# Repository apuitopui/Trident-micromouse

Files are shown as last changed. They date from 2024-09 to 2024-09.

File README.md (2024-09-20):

# TRIDENT - Classic size micromouse
Trident is a robotic project to compete in [classic size micromouse](https://www.ntf.or.jp/). 
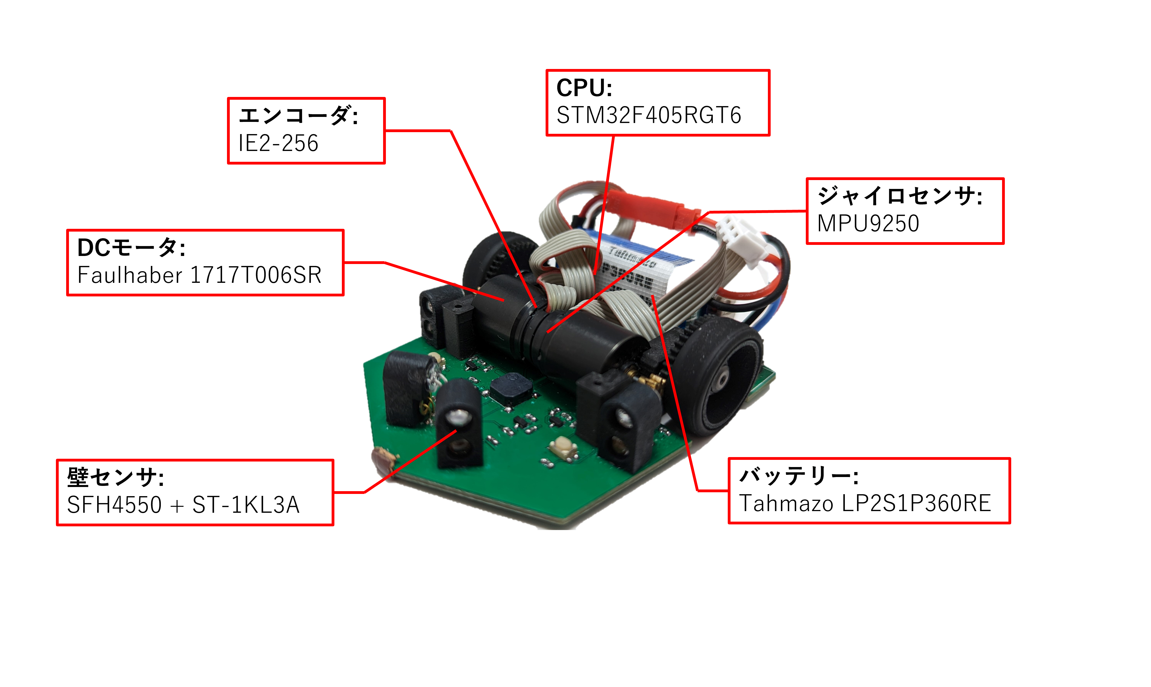
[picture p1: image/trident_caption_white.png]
Trident


## Circuit
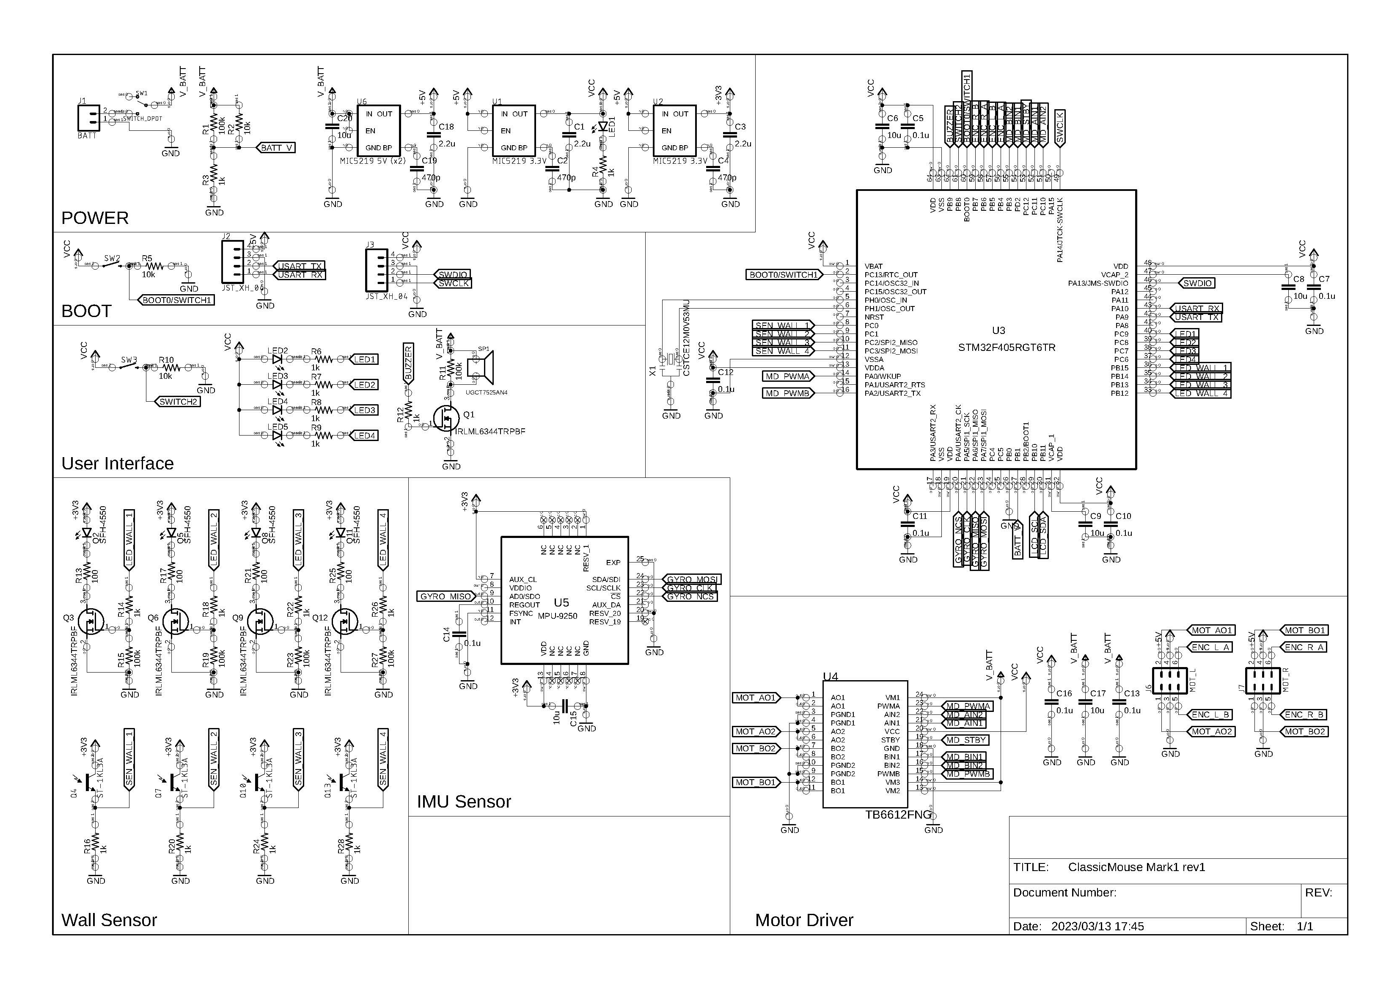
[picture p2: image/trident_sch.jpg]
Schematic


## Specification
|Specification|Value| 
|---|---|
|Size(W x L x H)| 70 x 84 x 30mm |
|Weight|About 100g|
|CPU|STM32F405RGT6|
|Battery|Tahmazo LP2S1P360RE|
|Motor|Faulhaber 1717T006SR|
|Encoder|IE2-256|
|Motor driver|TB6612FNG|
|Pinion|M0.5 9T Brass|
|Spur Gear|M0.5 42T PA12 MJF|
|Tire|Kyosho high grip tire|
|Gyro rensor|MPU9250|
|Wall sensor LED|SFH4500|
|Wall sensor Phototransistor| ST-1KL3A|

## Environment 
* IDE : STM32 Cube IDE
* EDA : Autodesk Eagle
* CAD : Autodesk Fusion

## Joined micromouse competition
|Date|Competition|Best time|Rank|
|---|---|---|---|
|2023/02/19|第43回全日本マイクロマウス大会|0:18.822|7|
|2023/09/24|第４０回マイクロマウス北陸信越地区大会|0:11.231|5|
|2023/11/12|第３９回マイクロマウス東日本地区大会|0:10.233|8|
|2023/12/09|第３７回全日本学生マイクロマウス大会|0:08.502|8|
|2023/02/18|第44回全日本マイクロマウス大会|0:09.356|14|

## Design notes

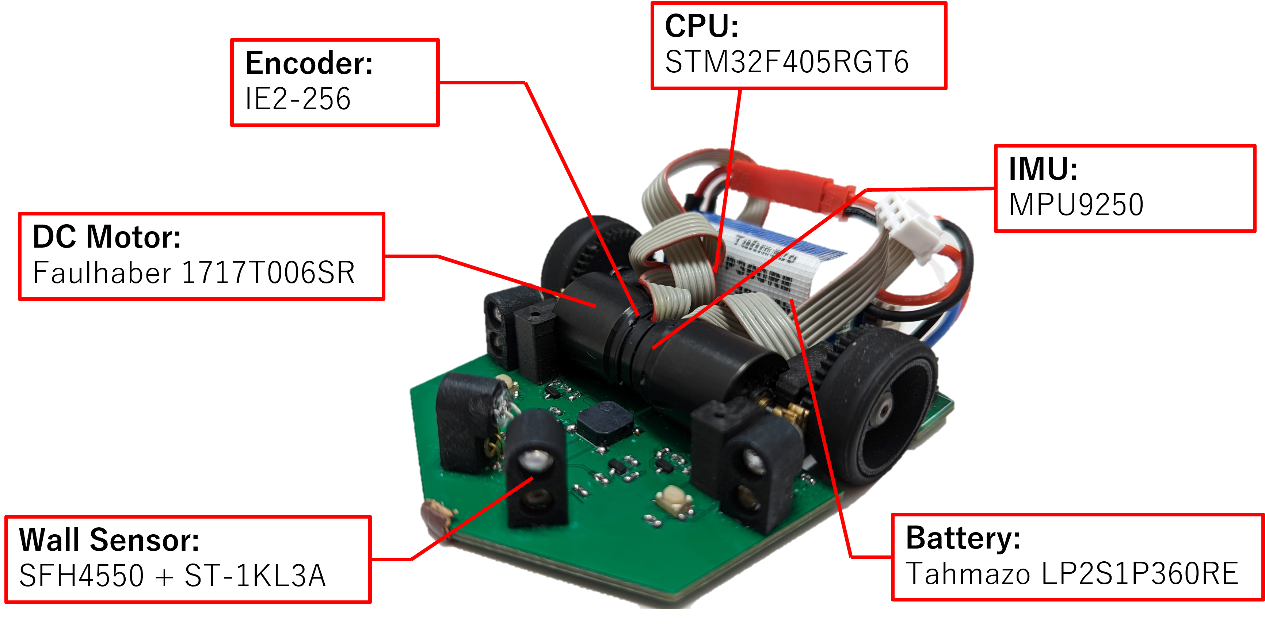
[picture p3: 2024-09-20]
image/trident_caption.png

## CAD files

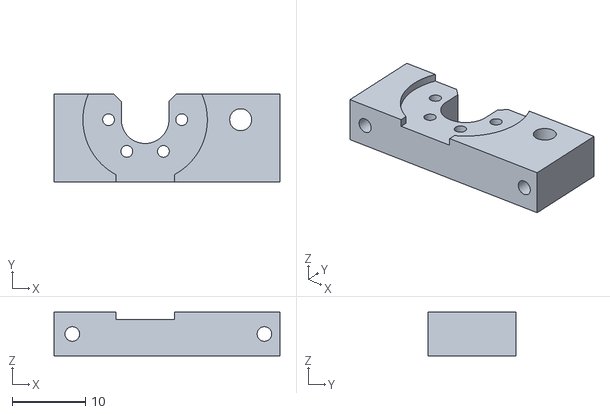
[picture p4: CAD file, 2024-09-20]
hardware/Trident M1 rev1 R.stl
30.9 x 12.0 x 6.00

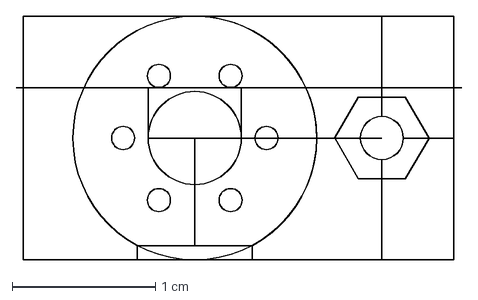
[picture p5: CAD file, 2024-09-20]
hardware/print2 v2.dxf
3.11 x 1.70 cm

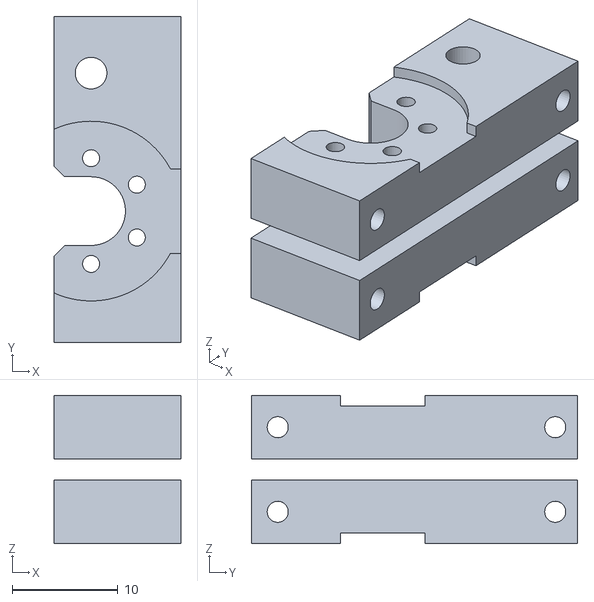
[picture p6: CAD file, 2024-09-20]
hardware/print3 v1.stl
12.0 x 30.9 x 14.0

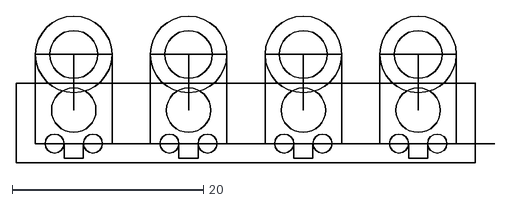
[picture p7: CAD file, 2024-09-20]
hardware/SensorMount.dxf
50.0 x 15.3

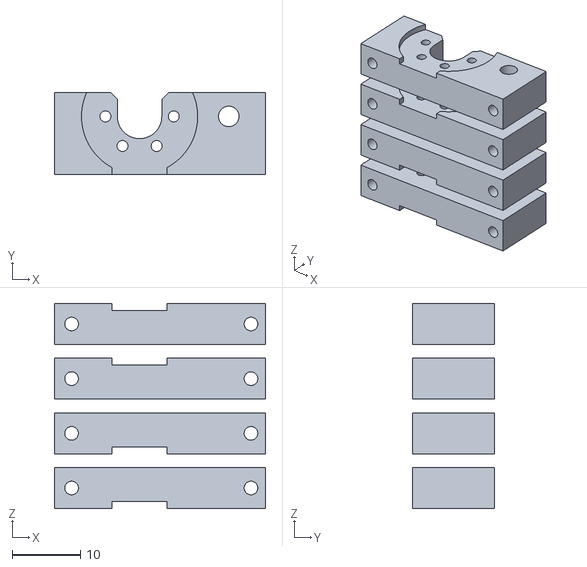
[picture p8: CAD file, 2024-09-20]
hardware/Trident M1 rev1Mount.stl
30.9 x 12.0 x 30.0

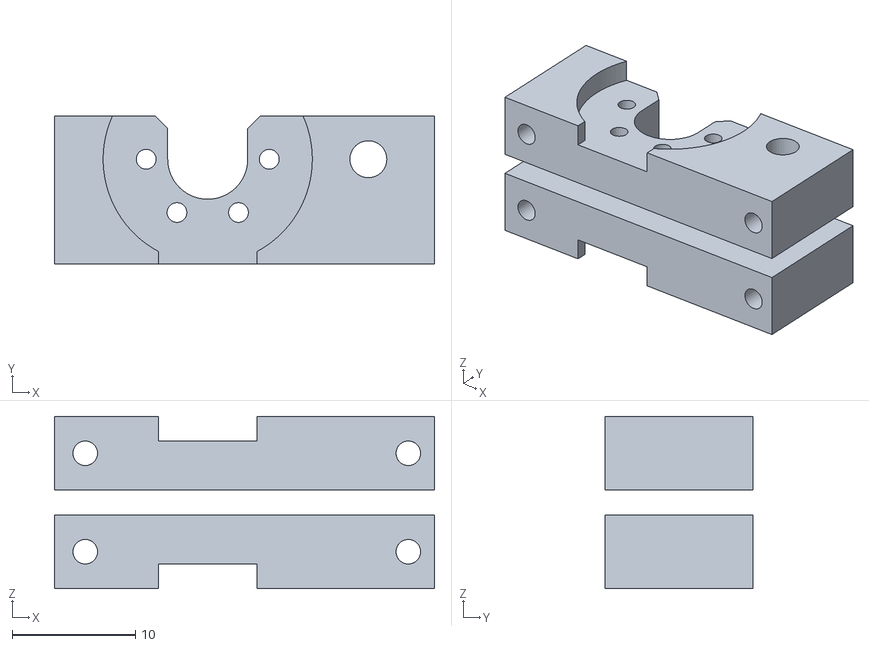
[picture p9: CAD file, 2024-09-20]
hardware/Trident M1 rev1 Mount2.stl
30.9 x 12.0 x 14.0

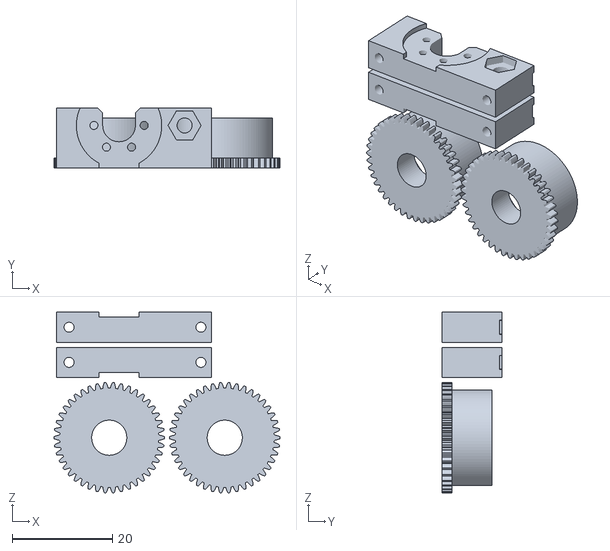
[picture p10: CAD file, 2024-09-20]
hardware/221201 - WheelMount.stl
45.0 x 12.0 x 36.0

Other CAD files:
hardware/無題 v2.dxf
hardware/Trident M1 rev1 L.stl
hardware/Trident M1 rev1 LR.stl
hardware/221204 - WheelMount.stl
hardware/Trident M1 rev1 Mount2.f3z
hardware/Trident Mark1 rev1 Mount.f3z

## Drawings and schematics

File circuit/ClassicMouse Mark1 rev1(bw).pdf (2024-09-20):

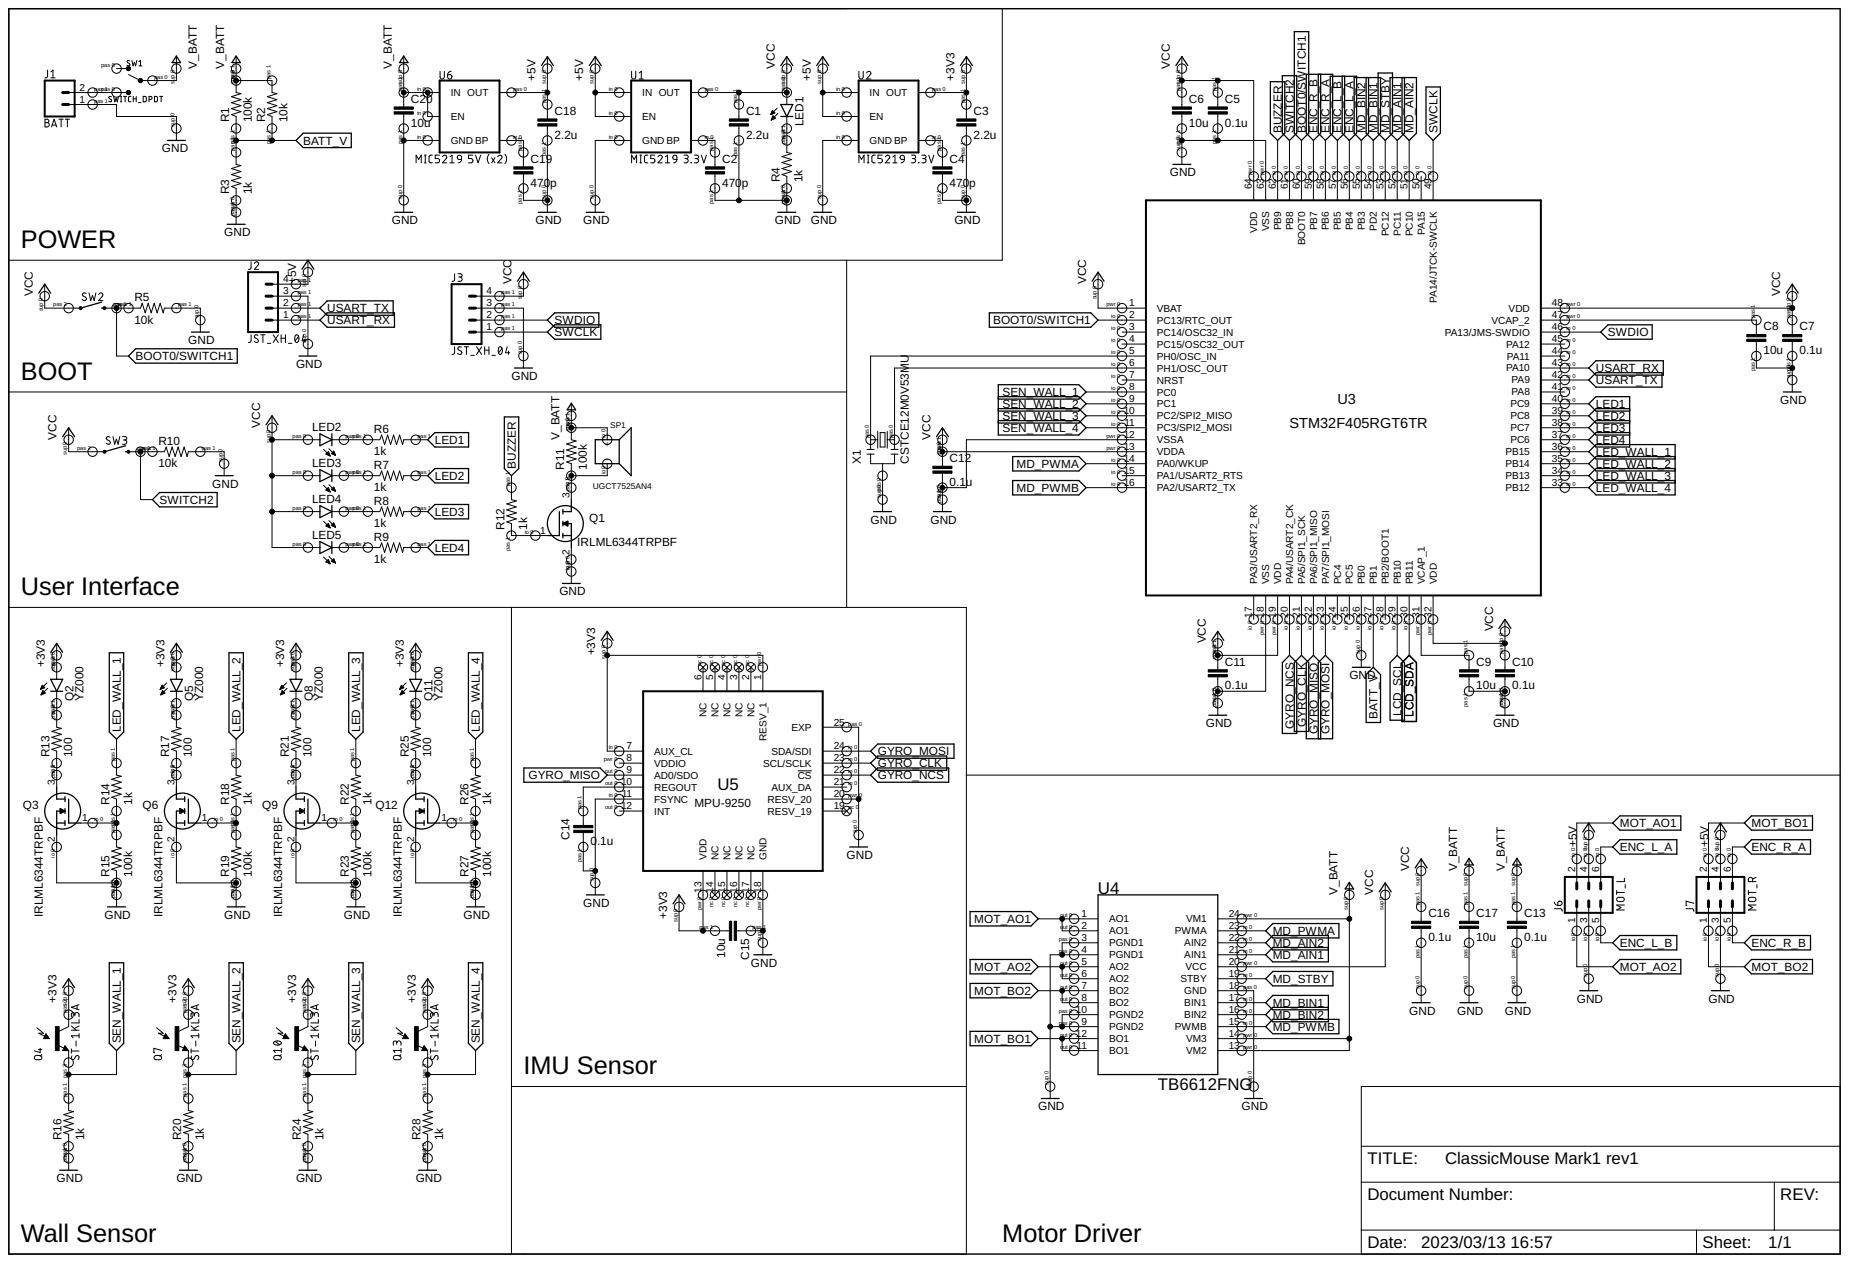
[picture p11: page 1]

pas 0 pas 0 pas 1 pas 1

pas 1 pas 1 sup 0 sup 0

io 0 io 0 pas 1 pas 1

pas 1 pas 1 pas 1 pas 1up 0

23 VM1 in 0 MD_PWMA

pas 0 | 21 AIN2 MD_AIN2 in 0

19 VCC in 0 MD_STBY

pas 1 pas 1up 0 pas 3 pas 2

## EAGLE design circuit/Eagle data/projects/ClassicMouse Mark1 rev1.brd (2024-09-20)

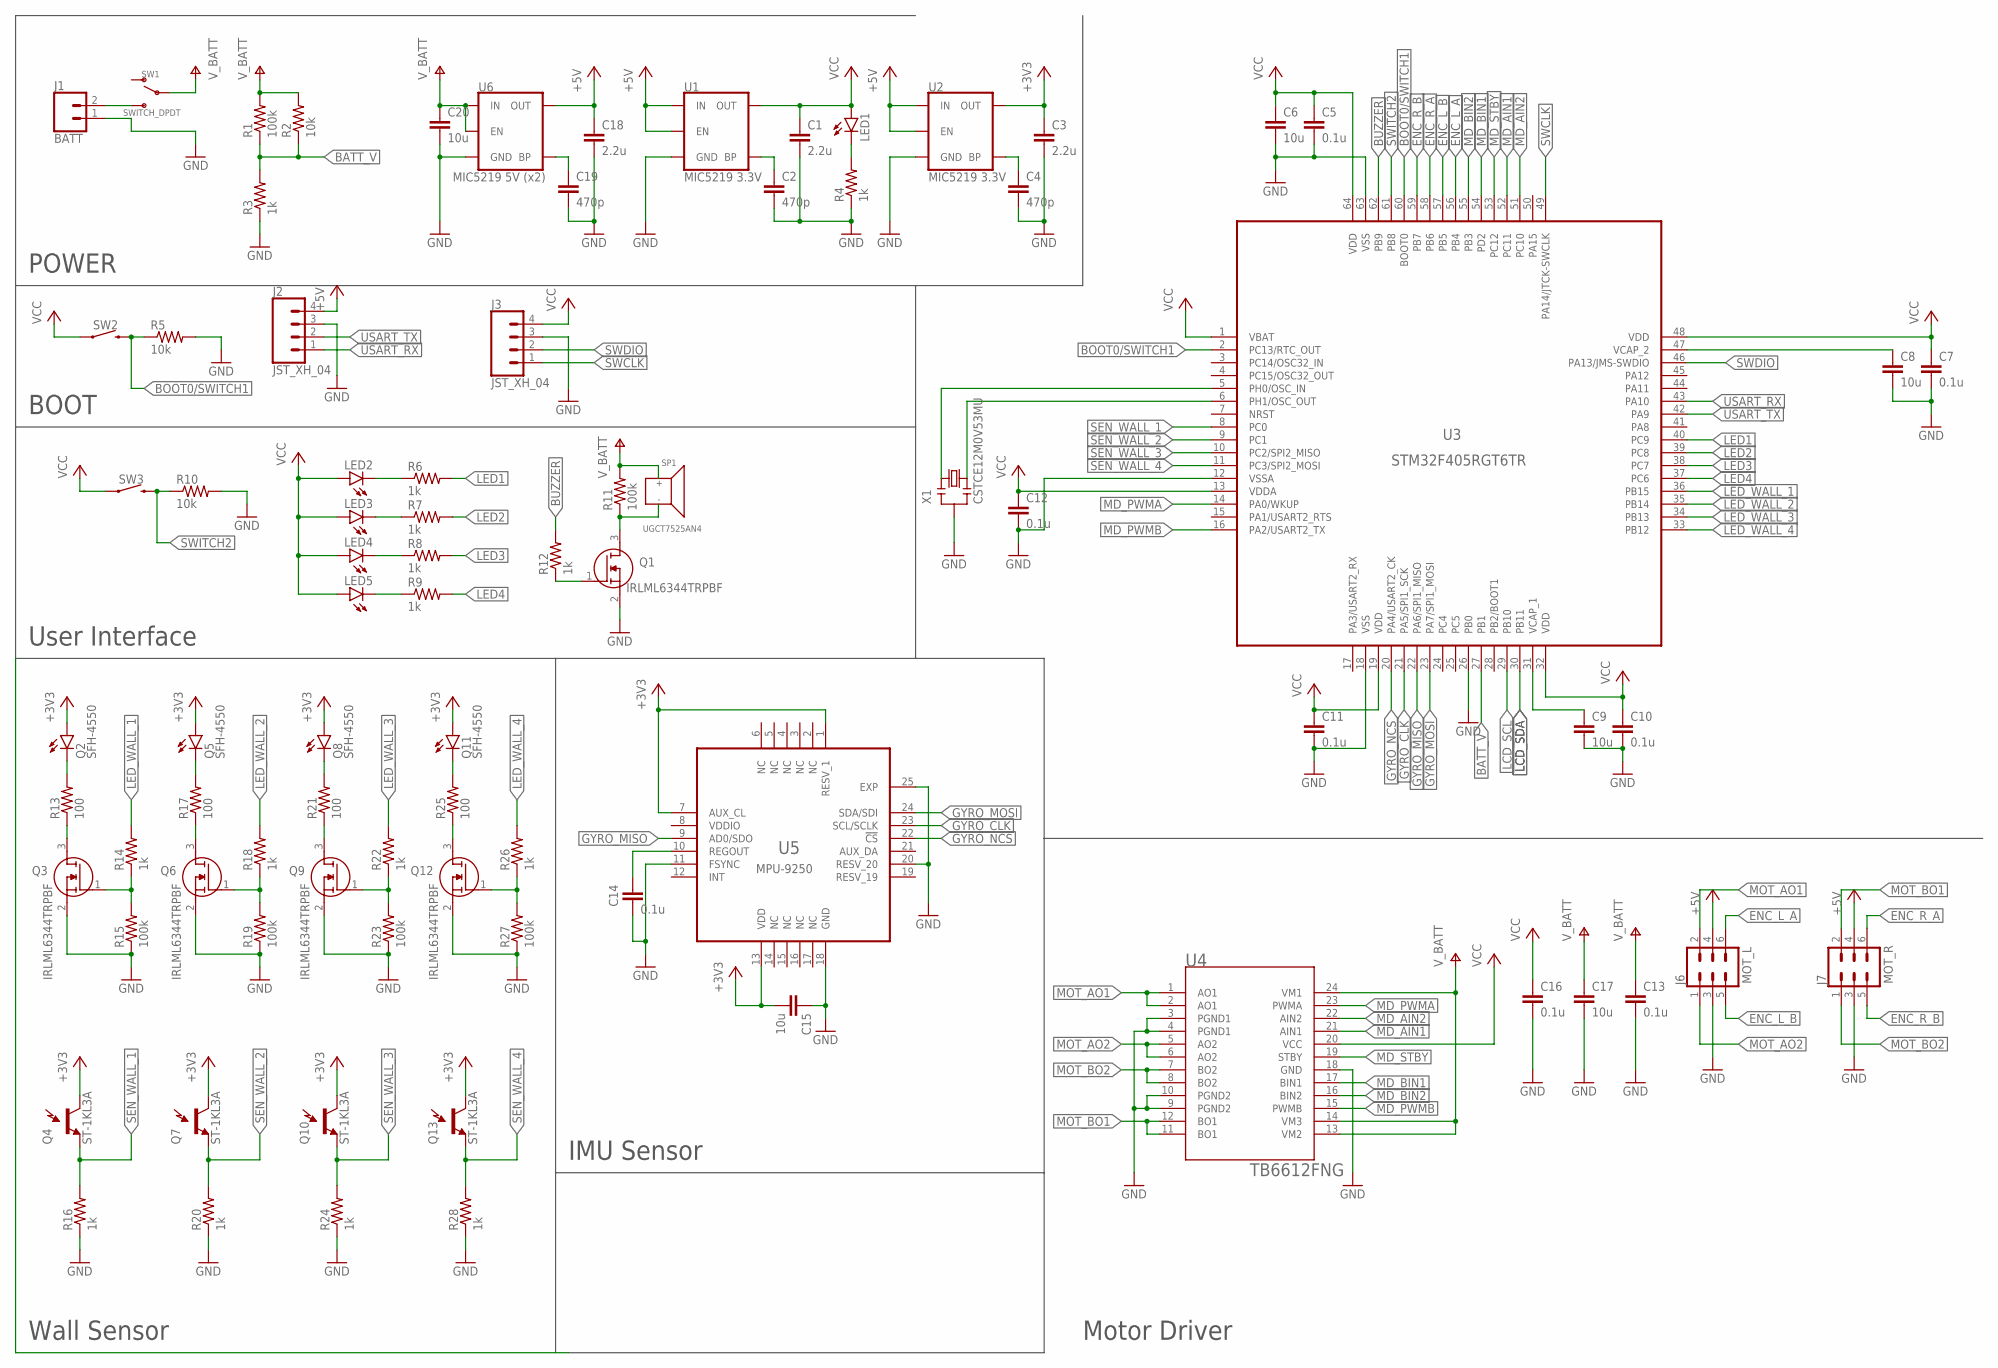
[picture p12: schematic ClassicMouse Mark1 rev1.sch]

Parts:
C1, C3, C18: 2.2u; C0603K
C2, C4, C19: 470p; C0603K
C5, C7, C10, C11, C12, C13, C14, C16: 0.1u; C0603K
C6, C8, C9: 10u; C0603K
C15, C17, C20: 10u; C1206
J1: BATT; JST-XH-02-PACKAGE-ROUND-PAD
J2, J3: JST_XH_04; JST-XH-04-PACKAGE-ROUND-PAD
J6: MOT_L; 2X3-NS
J7: MOT_R; 2X3-NS
LED1, LED2, LED3, LED4, LED5: LEDCHIPLED_0603; CHIPLED_0603
Q1, Q3, Q6, Q9, Q12: IRLML6344TRPBF; SOT95P260X110-3N
Q2, Q5, Q8, Q11: SFH-4550; CONN_02
Q4, Q7, Q10, Q13: ST-1KL3A; CONN_02
R1, R11, R15, R19, R23, R27: 100k; R0603
R2, R5, R10: 10k; R0603
R3, R4, R6, R7, R8, R9, R12, R14, R16, R18, R20, R22, R24, R26, R28: 1k; R0603
R13, R17, R21, R25: 100; R0603
SP1: UGCT7525AN4
SW1: SWITCH_DPDT
SW2, SW3: MOMENTARY-SWITCH-SPST-SMD-4.6X2.8MM; TACTILE_SWITCH_SMD_4.6X2.8MM
U1, U2: MIC5219 3.3V; SOT23-5
U3: STM32F405RGT6TR; QFP50P1200X1200X160-64N
U4: TB6612FNG; SOP65P760X160-24N
U5: MPU-9250; QFN40P300X300X105-25N
U6: MIC5219 5V (x2); SOT23-5
X1: CSTCE12M0V53MU; CSTCE12M0V53

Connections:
+3V3: C3.1, C15.2, Q2.+ (A), Q4.+ (C1), Q5.+ (A), Q7.+ (C1), Q8.+ (A), Q10.+ (C1), Q11.+ (A), Q13.+ (C1), U2.5 (OUT), U5.1 (RESV_1), U5.7 (AUX_CL), U5.13 (VDD)
+5V: C18.1, J2.4, J6.4, J7.4, U1.1 (IN), U1.3 (EN), U2.1 (IN), U2.3 (EN), U6.5 (OUT)
BATT_V: R1.1, R2.1, R3.2, U3.27 (PB1)
BOOT0/SWITCH1: R5.1, SW2.3 (2), SW2.4 (2), U3.2 (PC13/RTC_OUT), U3.60 (BOOT0)
BUZZER: R12.2, U3.62 (PB9)
ENC_L_A: J6.6, U3.56 (PB4)
ENC_L_B: J6.5, U3.57 (PB5)
ENC_R_A: J7.6, U3.58 (PB6)
ENC_R_B: J7.5, U3.59 (PB7)
GND: C1.2, C2.2, C3.2, C4.2, C5.2, C6.2, C7.2, C8.2, C9.2, C10.2, C11.2, C12.2, C13.2, C14.2, C15.1, C16.2, C17.2, C18.2, C19.2, C20.2, J1.1, J2.3, J3.3, J6.3, J7.3, Q1.2 (S), Q3.2 (S), Q6.2 (S), Q9.2 (S), Q12.2 (S), R3.1, R4.1, R5.2, R10.2, R15.1, R16.1, R19.1, R20.1, R23.1, R24.1, R27.1, R28.1, U1.2 (GND), U2.2 (GND), U3.12 (VSSA), U3.18 (VSS), U3.26 (PB0), U3.63 (VSS), U4.3 (PGND1), U4.4 (PGND1), U4.9 (PGND2), U4.10 (PGND2), U4.18 (GND), U5.11 (FSYNC), U5.18 (GND), U5.20 (RESV_20), U5.25 (EXP), U6.2 (GND), X1.2
GYRO_CLK: U3.21 (PA5/SPI1_SCK), U5.23 (SCL/SCLK)
GYRO_MISO: U3.22 (PA6/SPI1_MISO), U5.9 (AD0/SDO)
GYRO_MOSI: U3.23 (PA7/SPI1_MOSI), U5.24 (SDA/SDI)
GYRO_NCS: U3.20 (PA4/USART2_CK), U5.22 (!CS)
LCD_SCL: U3.29 (PB10)
LCD_SDA: U3.30 (PB11)
LED1: R6.2, U3.40 (PC9)
LED2: R7.2, U3.39 (PC8)
LED3: R8.2, U3.38 (PC7)
LED4: R9.2, U3.37 (PC6)
LED_WALL_1: R14.2, U3.36 (PB15)
LED_WALL_2: R18.2, U3.35 (PB14)
LED_WALL_3: R22.2, U3.34 (PB13)
LED_WALL_4: R26.2, U3.33 (PB12)
MD_AIN1: U3.52 (PC11), U4.21 (AIN1)
MD_AIN2: U3.51 (PC10), U4.22 (AIN2)
MD_BIN1: U3.54 (PD2), U4.17 (BIN1)
MD_BIN2: U3.55 (PB3), U4.16 (BIN2)
MD_PWMA: U3.14 (PA0/WKUP), U4.23 (PWMA)
MD_PWMB: U3.16 (PA2/USART2_TX), U4.15 (PWMB)
MD_STBY: U3.53 (PC12), U4.19 (STBY)
MOT_AO1: J6.2, U4.1 (AO1), U4.2 (AO1)
MOT_AO2: J6.1, U4.5 (AO2), U4.6 (AO2)
MOT_BO1: J7.2, U4.11 (BO1), U4.12 (BO1)
MOT_BO2: J7.1, U4.7 (BO2), U4.8 (BO2)
unnamed: J1.2, SW1.3 (S), SW1.6 (S)
unnamed: C2.1, U1.4 (BP)
unnamed: U3.6 (PH1/OSC_OUT), X1.3
unnamed: C4.1, U2.4 (BP)
unnamed: U3.5 (PH0/OSC_IN), X1.1
unnamed: C8.1, U3.47 (VCAP_2)
unnamed: C9.1, U3.31 (VCAP_1)
unnamed: LED1.C, R4.2
unnamed: Q1.3 (D), R11.1, SP1.2 (GND)
unnamed: Q1.1 (G), R12.1
unnamed: Q2.- (C), R13.2
unnamed: Q3.3 (D), R13.1
unnamed: Q5.- (C), R17.2
unnamed: Q3.1 (G), R14.1, R15.2
unnamed: Q6.3 (D), R17.1
unnamed: Q6.1 (G), R18.1, R19.2
unnamed: Q8.- (C), R21.2
unnamed: Q9.3 (D), R21.1
unnamed: Q9.1 (G), R22.1, R23.2
unnamed: Q11.- (C), R25.2
unnamed: Q12.3 (D), R25.1
unnamed: Q12.1 (G), R26.1, R27.2
unnamed: LED2.C, R6.1
unnamed: LED3.C, R7.1
unnamed: C14.1, U5.10 (REGOUT)
unnamed: C19.1, U6.4 (BP)
unnamed: LED4.C, R8.1
unnamed: LED5.C, R9.1
SEN_WALL_1: Q4.- (E1), R16.2, U3.8 (PC0)
SEN_WALL_2: Q7.- (E1), R20.2, U3.9 (PC1)
SEN_WALL_3: Q10.- (E1), R24.2, U3.10 (PC2/SPI2_MISO)
SEN_WALL_4: Q13.- (E1), R28.2, U3.11 (PC3/SPI2_MOSI)
SWCLK: J3.1, U3.49 (PA14/JTCK-SWCLK)
SWDIO: J3.2, U3.46 (PA13/JMS-SWDIO)
SWITCH2: R10.1, SW3.3 (2), SW3.4 (2), U3.61 (PB8)
USART_RX: J2.1, U3.43 (PA10)
USART_TX: J2.2, U3.42 (PA9)
V+: C13.1, C17.1, C20.1, R1.2, R2.2, R11.2, SP1.1 (V), SW1.2, SW1.5, U4.13 (VM2), U4.14 (VM3), U4.24 (VM1), U6.1 (IN), U6.3 (EN)
VCC: C1.1, C5.1, C6.1, C7.1, C10.1, C11.1, C12.1, C16.1, J3.4, LED1.A, LED2.A, LED3.A, LED4.A, LED5.A, SW2.1, SW2.2 (1), SW3.1, SW3.2 (1), U1.5 (OUT), U3.1 (VBAT), U3.13 (VDDA), U3.19 (VDD), U3.32 (VDD), U3.48 (VDD), U3.64 (VDD), U4.20 (VCC)
VDDIO: U5.8 (VDDIO)

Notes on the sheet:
POWER
BOOT
User Interface
Wall Sensor
IMU Sensor
Motor Driver

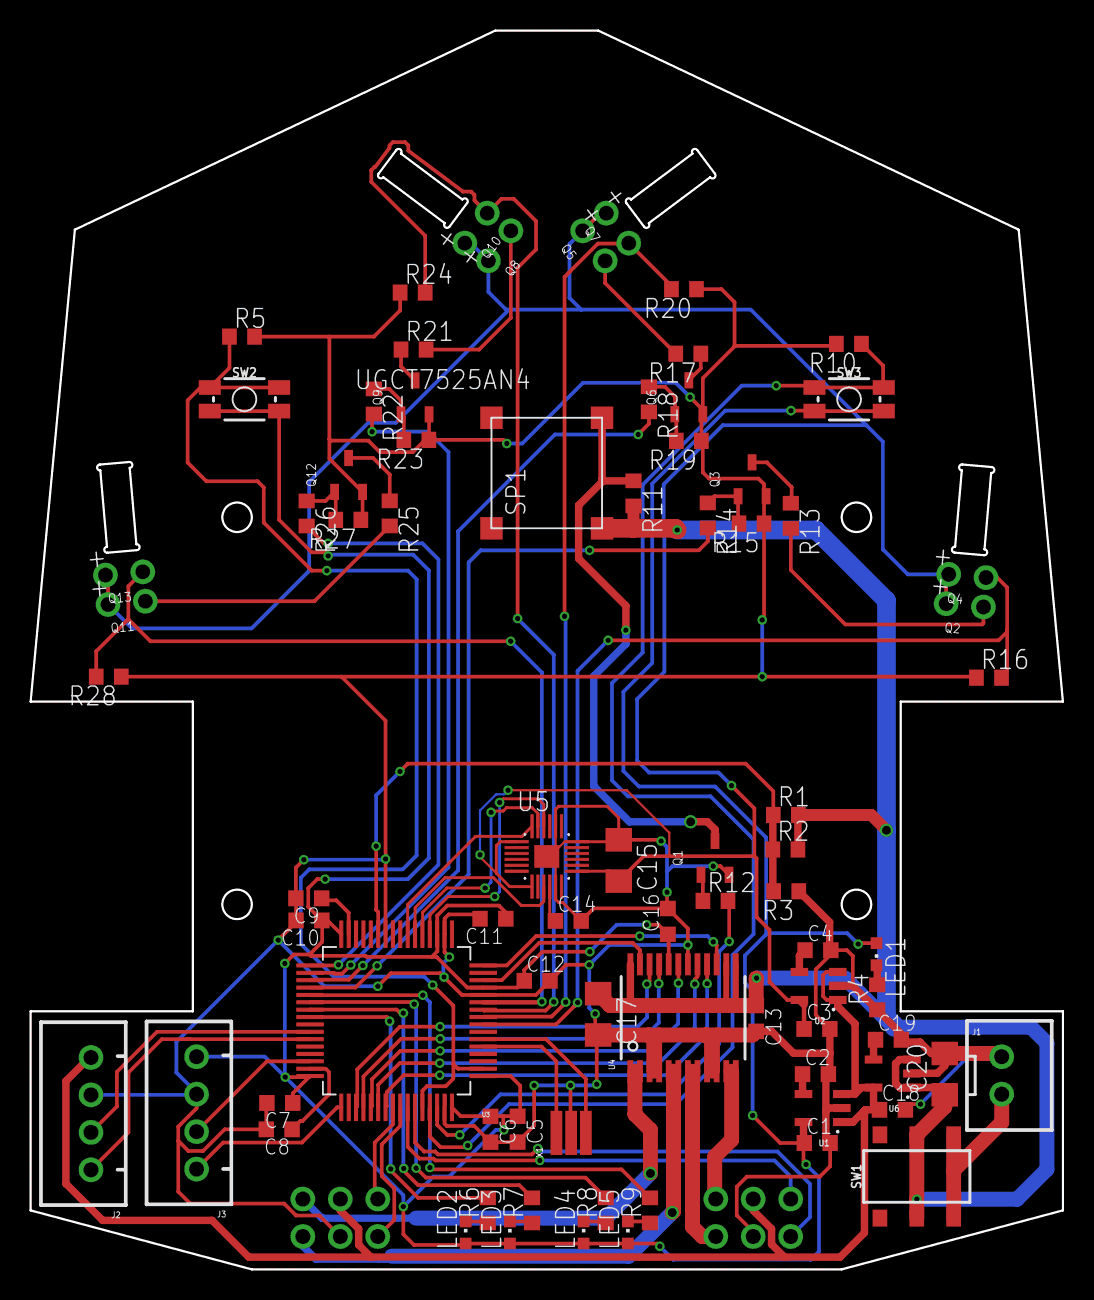
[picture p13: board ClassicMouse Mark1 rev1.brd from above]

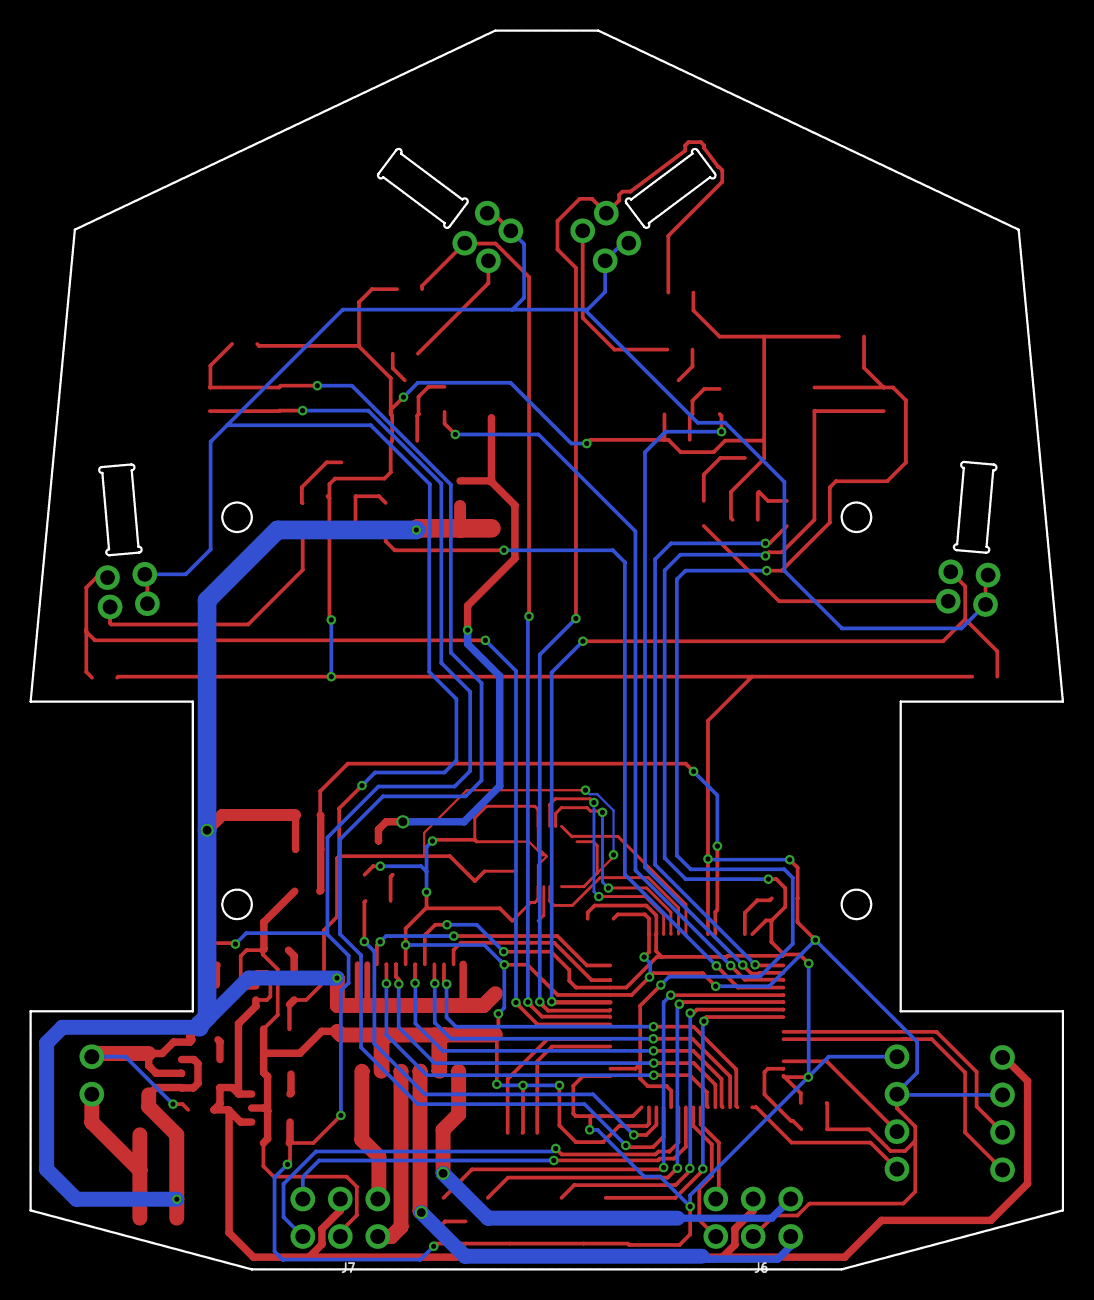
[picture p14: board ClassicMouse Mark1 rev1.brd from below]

Board: 2 copper layers, 70.0 x 84.0 mm, 82 parts (2 on the bottom side), 72 nets.

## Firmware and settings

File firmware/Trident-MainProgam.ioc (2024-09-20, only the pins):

Mcu.UserName=STM32F405RGTx
PA0-WKUP.GPIO_Label=MOT_PWMA
PA0-WKUP.Signal=S_TIM2_CH1_ETR
PA10.Signal=USART1_RX
PA13.Signal=SYS_JTMS-SWDIO
PA14.Signal=SYS_JTCK-SWCLK
PA2.GPIO_Label=MOT_PWMB
PA2.Signal=S_TIM2_CH3
PA4.GPIO_Label=GYRO_NCS
PA4.Signal=GPIO_Output
PA5.GPIO_Label=GYRO_SCK
PA5.Signal=SPI1_SCK
PA6.GPIO_Label=GYRO_MISO
PA6.Signal=SPI1_MISO
PA7.GPIO_Label=GYRO_MOSI
PA7.Signal=SPI1_MOSI
PA9.Signal=USART1_TX
PB1.GPIO_Label=BATT_V
PB1.Signal=ADCx_IN9
PB12.GPIO_Label=LED_WALL_FL
PB12.Signal=GPIO_Output
PB13.GPIO_Label=LED_WALL_L
PB13.Signal=GPIO_Output
PB14.GPIO_Label=LED_WALL_R
PB14.Signal=GPIO_Output
PB15.GPIO_Label=LED_WALL_FR
PB15.Signal=GPIO_Output
PB3.GPIO_Label=MOT_BIN2
PB3.Signal=GPIO_Output
PB4.GPIO_Label=ENC_L_A
PB4.Signal=S_TIM3_CH1
PB5.GPIO_Label=ENC_L_B
PB5.Signal=S_TIM3_CH2
PB6.GPIO_Label=ENC_R_A
PB6.Signal=S_TIM4_CH1
PB7.GPIO_Label=ENC_R_B
PB7.Signal=S_TIM4_CH2
PB8.GPIO_Label=SW_R
PB8.Signal=GPIO_Input
PB9.GPIO_Label=BUZZER
PB9.Signal=S_TIM11_CH1
PC0.GPIO_Label=SEN_WALL_FR
PC0.Signal=ADCx_IN10
PC1.GPIO_Label=SEN_WALL_R
PC1.Signal=ADCx_IN11
PC10.GPIO_Label=MOT_AIN2
PC10.Signal=GPIO_Output
PC11.GPIO_Label=MOT_AIN1
PC11.Signal=GPIO_Output
PC12.GPIO_Label=MOT_STBY
PC12.Signal=GPIO_Output
PC13-ANTI_TAMP.GPIO_Label=SW_L
PC13-ANTI_TAMP.Signal=GPIO_Input
PC2.GPIO_Label=SEN_WALL_L
PC2.Signal=ADCx_IN12
PC3.GPIO_Label=SEN_WALL_FL
PC3.Signal=ADCx_IN13
PC6.GPIO_Label=LED1
PC6.Signal=GPIO_Output
PC7.GPIO_Label=LED2
PC7.Signal=GPIO_Output
PC8.GPIO_Label=LED3
PC8.Signal=GPIO_Output
PC9.GPIO_Label=LED4
PC9.Signal=GPIO_Output
PD2.GPIO_Label=MOT_BIN1
PD2.Signal=GPIO_Output
PH0-OSC_IN.Signal=RCC_OSC_IN
PH1-OSC_OUT.Signal=RCC_OSC_OUT

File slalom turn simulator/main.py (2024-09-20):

##################################################
# マイクロマウス用シミュレータ
#                           2022/07/06 K. Richardo
###################################################

#################################
# ライブラリのインポート
#################################
import sys
import os
import math
import numpy as np
import csv

import matplotlib
import matplotlib.pyplot as plt
from matplotlib.backends.backend_qt5agg import FigureCanvasAgg as FigureCanvas
from matplotlib.figure import Figure

from PyQt5 import QtWidgets, QtCore, QtGui, uic
from PyQt5.QtCore import QThread, QObject, pyqtSignal

import operator
import serial
import serial.tools.list_ports
from datetime import datetime

#################################
# グローバル変数定義
#################################
uiMainWindow, _= uic.loadUiType('simulator.ui')

#################################
# Windowのクラス
#################################
class mainWindow(QtWidgets.QMainWindow, uiMainWindow):
    # -------------------------------
    # 初期化
    def __init__(self):
        # Windowの表示
        QtWidgets.QMainWindow.__init__(self)
        uiMainWindow.__init__(self)
        self.setupUi(self)

        # Baudrate 115200にデフォルト表示
        # 0: 9600, 1: 19200, 2: 38400, 3: 57600, 4: 115200
        self.CBoxBaudrate.setCurrentIndex(4)

        # 使用可能COMポートを表示
        self.get_available_com_ports()

        # ボタンを関数に接続
        self.BPortRefresh.clicked.connect(self.BPortRefresh_Clicked)
        self.BConnect.clicked.connect(self.BConnect_Clicked)

    # -------------------------------
    # 使用可能COMポート取得
    def get_available_com_ports(self):
        self.CBoxPort.clear()

        self.available_ports_all = list( serial.tools.list_ports.comports() )
        self.available_ports = [port for port in self.available_ports_all if port[2] != 'n/a']
        self.available_ports.sort(key=operator.itemgetter(1))

        for port, desc, _ in self.available_ports:
            self.CBoxPort.addItem(port)

    # -------------------------------
    # COMポートを再読み込み
    def BPortRefresh_Clicked(self):
        self.get_available_com_ports()

    # -------------------------------
    # COMポートに接続
    def BConnect_Clicked(self):
        global uart
        (self.selected_port, _, _) = self.available_ports[ self.CBoxPort.currentIndex() ]
        self.selected_baudrate = self.CBoxBaudrate.currentText()

        # Opening COM Port
        try:
            print("Opening %s" % self.selected_port)
            print("Baud rate %s" % self.selected_baudrate)
            uart = serial.Serial(
                self.selected_port,
                self.selected_baudrate,
                timeout = 1,
                bytesize = serial.EIGHTBITS,
                parity = serial.PARITY_NONE,
                stopbits = serial.STOPBITS_ONE
            )
            self.LConnStatus.setText("Connected")

        except serial.SerialException:
            print("[!] Unable to open %s." % self.selected_port)
            self.LConnStatus.setText("Error")
            exit(-1)
        
        uart.write(b'"1"')
        while True:
            c = uart.read()
            print(c)
            if c == 'end':
                break
        
        uart.close()

        # CSV出力
        # timestamp = datetime.now().strftime("%Y-%m-%d %H:%M:%S")
        # output_dir = "_output/" + timestamp
        # output_csv_dir = output_dir + "data.csv"
        # with open( output_csv_dir, 'w', encoding='UTF8', newline='' ) as f:
        #     writer = csv.writer(f)
            
        
        

#################################
# スレッドのクラス
#################################
    
#################################
# main関数
#################################
if __name__ == '__main__':
    app = QtWidgets.QApplication(sys.argv)
    window = mainWindow()
    window.show()
    app.exec()
